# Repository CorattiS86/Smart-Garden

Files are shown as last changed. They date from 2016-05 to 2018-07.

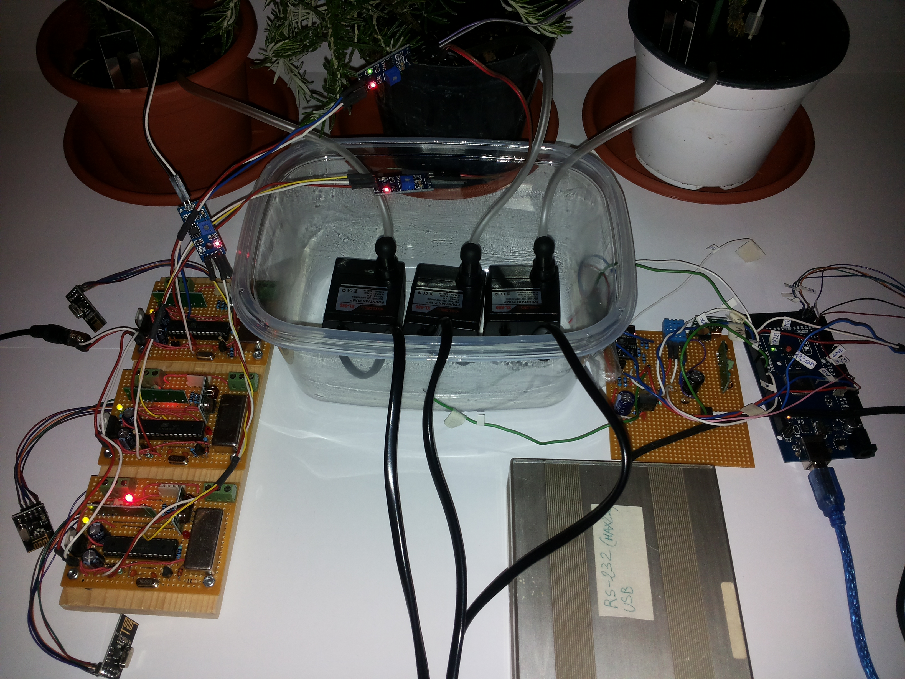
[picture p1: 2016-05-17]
Photos/system_2.jpg

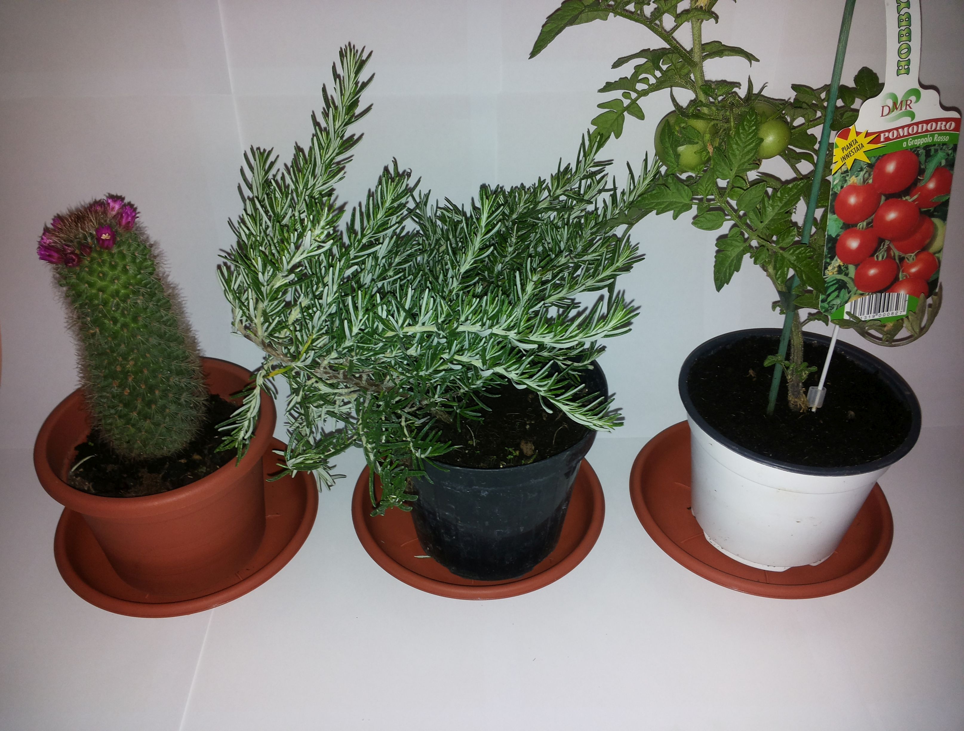
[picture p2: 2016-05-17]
Photos/plants.jpg

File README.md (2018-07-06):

# Smart-Garden
Pervasive Systems 2016 - DIAG "La Sapienza"
Stefano Coratti & Massimo Perri

In this repository there is all the material that describe how it was possible to build a system able to manage the watering of a garden.

The garden consists of 3 plants, for our choice we select:
 - Cactus plant
 - Rosemary plant
 - Tomato plant

The reason of such 3 plants is that they present 3 different characteristics from the point of view of watering.

For watering we decided to use flow irrigation. 
The biggest challenge in flow irrigation is accurately determining how much and when to water.

Based on a reasearch, that you can find in the follow link 

  "http://ucanr.edu/sites/scmg/files/30917.pdf" 
  
it is possible to see what influence irrigation for several kind of plant:
  - ET° (Evapotranspiration) factor
  - Crop coefficent
  - Density
  - Exposure factor
  - Planted area
  - Irrigation efficency
 
EVAPOTRANSPIRATION
Is the combined effect of soil water evaporation and plant water transpiration in the sorrounding environment, and values 
are provided in tables based on months for a specific location (latitude, proximity to the sea, etc...), referred 
to a reference crop ET° (grass).
We have found the table for own plant considering a mediterranean, center-south of italy environment.  

CROP COEFFICIENT
Crop coefficients, or species factors range from 0.1 to 0.9 and are
divided into four categories:
  - Very low      < 0.1 (10% of ET°)
  - Low       0.1 - 0.3 (10-30%)
  - Moderate  0.4 - 0.6 (40-60%)
  - High      0.7 - 0.9 (70-90%) 
 
PLANTING DENSITY
The planting density factor ranges in value from 0.5 to 1.3.
This range is separated into three categories:
  - Low—sparse                 0.5 - 0.9
  - Average—moderate coverage  1.0
  - High--complete coverage    1.1 - 1.3  
 
EXPOSURE FACTOR
The microclimate or exposure factor ranges from 0.5 to 1.4, and is divided into three categories: 
Average is open field, lowmoderate wind, part sun. Higher winds and greater exposure take a
higher factor, and a protected, shady location would use a lower factor.
  - Low     0.5 - 0.9
  - Average 1.0
  - High    1.1 - 1.4 
 
IRRIGATION EFFICENCY
Is related to the efficency of the kind of water erogator, in own implementation we assume 0.9 (90%) of efficency,
because the erogator hose is placed close to the roots.
 
Returning to what was said before, the choice of 3 plants is due to the fact that they have different values
of CROP EFFICENT and PLANTING DENSITY

|plant |crop coeff. | plant density | exposure factor | irrigation efficency |
|---|---|---|---|---|
| cactus | 0.2 | 1.0 | 1.0 | 0.9 | 
| rosemary  | 0.5 | 1.0 | 1.0 | 0.9 |
| tomato | 0.9 | 1.0 | 1.0 | 0.9 |

from which it is established a formula that says the amount of water necessary for the plant for a month

  (ET° x crop coeff. x density x exposure factor x planted area x .623) / (Irrigation efficiency)

such formula expresses the amount of water in gallons we translate such formula in liters, 
and use a conversion to compute daily amount of water. 

We use such informations to independently configure the 3 plants to obtain for each one an efficiently irrigation
using the least amount of water possible. 

Author
-----------------
Coratti Stefano

coratti.s86@gmail.com

https://www.linkedin.com/in/stefano-coratti-83005a85/

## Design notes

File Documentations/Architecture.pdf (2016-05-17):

## SMART GARDEN PROJECT

### Pervasive System 2016 – DIAG “La Sapienza” Stefano Coratti & Massimo Perri

ARCHITECTURE:

The Smart Garden is a system composed by many elaboration/processing nodes or station that are within a garden scenario with plants, where each plant has its own ‘plant computer’ and there is a unique ‘master’ station in the garden.

In the demo implementation a single master and three slave stations are provided. The stations create a wireless network, where each station has an address and plant stations can interact and exchange messages with the central master station. Master station transmit broadcast messages to all the slaves in the network and receive messages from the single slave stations to it.

The scope of the master station is providing timing broadcast sync messages and weather data, using readings from a number of sensors that capture the relevant environmental values (atmospheric pressure, temperature, humidity, light intensity) to the slave/plant stations.

Plant stations do synchronize with the master, receive data from it and perform each their own calculation and the intelligent decision algorithm, with as inputs the weather data received from the master and their own configuration, that depends on the kind of plants they provide water.

The general idea is that the master periodically sends a sync message with weather and configuration information to the slaves; the slaves keep receiving until they got the master sync message, extract info and use them as input to their internal watering algorithm, along with slave station specific configuration. On the base of results of the watering algorithm each slave station provide or not provide water to the associated plant and, also, calculate the right volume amount of water to use, issuing commands to a submersible water pump that pumps up the water to the plant from a tank.

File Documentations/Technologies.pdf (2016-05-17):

## SMART GARDEN PROJECT

### Pervasive System 2016 – DIAG “La Sapienza” Stefano Coratti & Massimo Perri

TECHNOLOGIES:

We used the following technologies in the Smart Garden project

Arduino, both the hardware platform (in the specific 1 Arduino Mega 2560 and 3 custom made Arduino-standalone ATMEGA328P@16Mhz) and the software one, means the Arduino IDE and programming language https://www.arduino.cc/

USPASP programmer hardware/driver , used to physically made in circuit programming on the slave stations by Arduino IDE http://www.fischl.de/usbasp/

USB-RS232+MAX232 interface & logic level converter to provide extra serial communication with the Arduino Mega for diagnostic and debug purposes https://en.wikipedia.org/wiki/MAX232

Blynk to provide in the cloud data forwarding and client app to Android/IOS devices, used to visualize actual data from the smart garden, including soil humidity levels at the plants http://www.blynk.cc/

ThingSpeak service for IoT to provide in the cloud data collection and graphic visualization of collected data points and also to trigger a react for generating email alerts using PushingBox web service https://thingspeak.com/

PushingBox service for IoT, an Internet based service to provide email sending from devices, in our case PushingBox actions are controlled directly by events captured at ThingSpeak data collection facility https://www.pushingbox.com/

ExtremeAVRBurner or avrdude AVR programming software: http://extremeelectronics.co.in/avrtutorials/gui-software-for-usbasp-based-usb-avr-programmers/ (http://extremeelectronics.co.in/avr-tutorials/gui-software-for-usbasp-based-usb-avr-programmers/) , http://www.nongnu.org/avrdude/ use one of these tools to program just once the ATmega328Ps fuse bits (required to make them run at 16Mhz clock external oscillator)

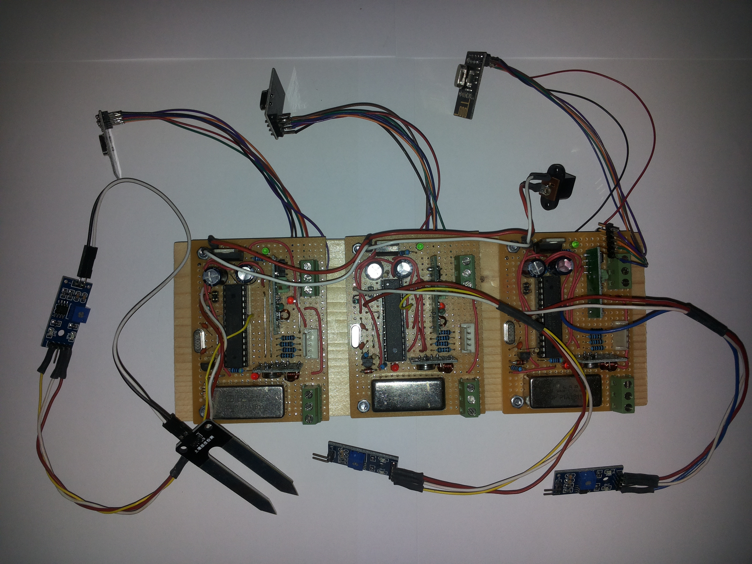
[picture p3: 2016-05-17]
Photos/slaves.jpg

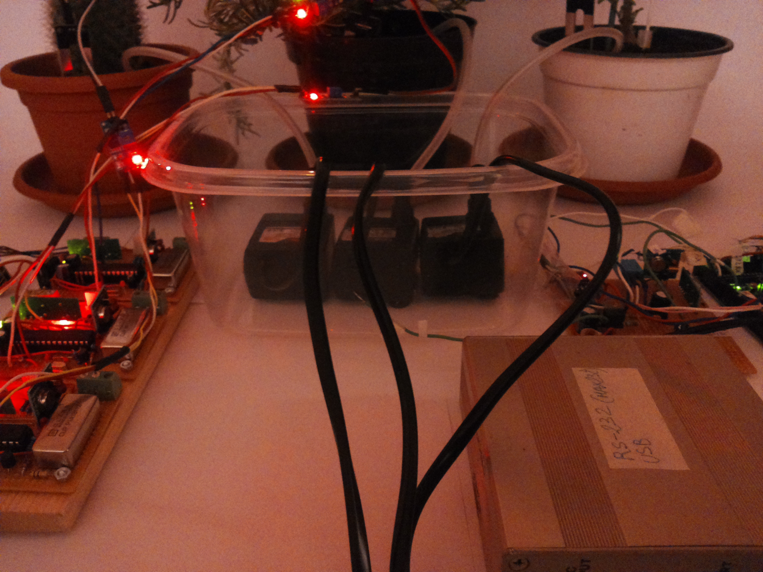
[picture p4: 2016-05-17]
Photos/system_3.jpg

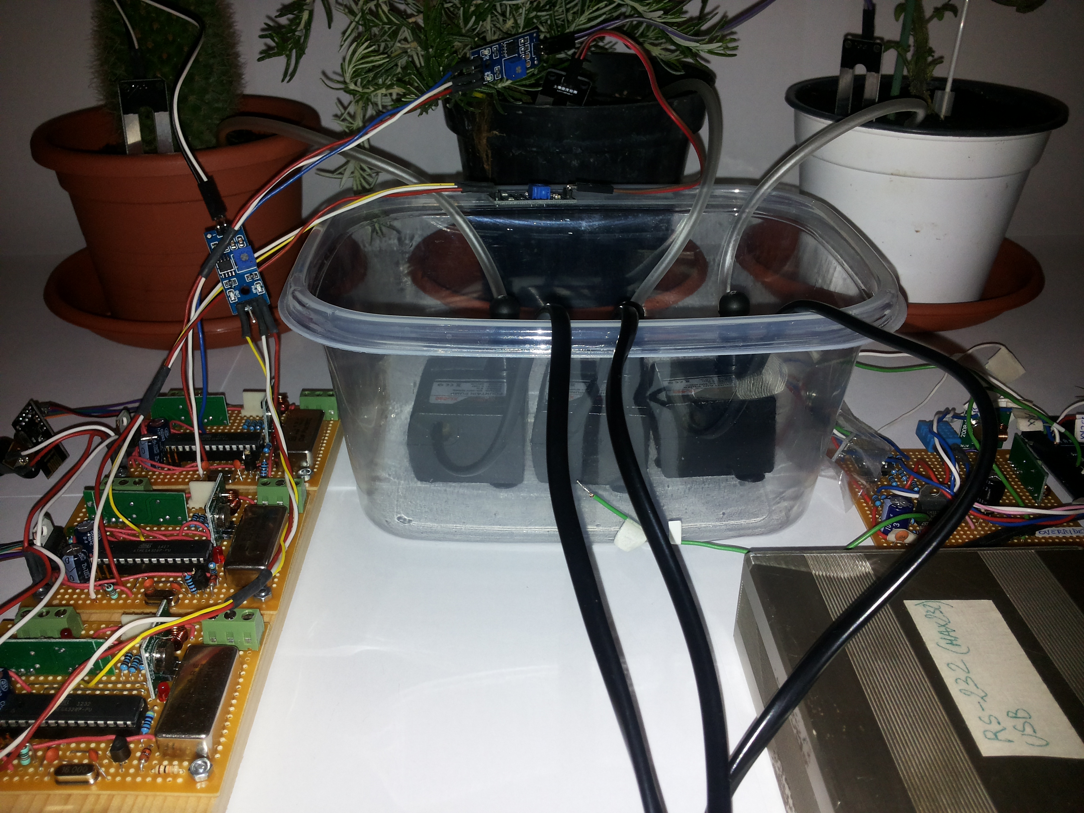
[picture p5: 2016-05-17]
Photos/system_1.jpg

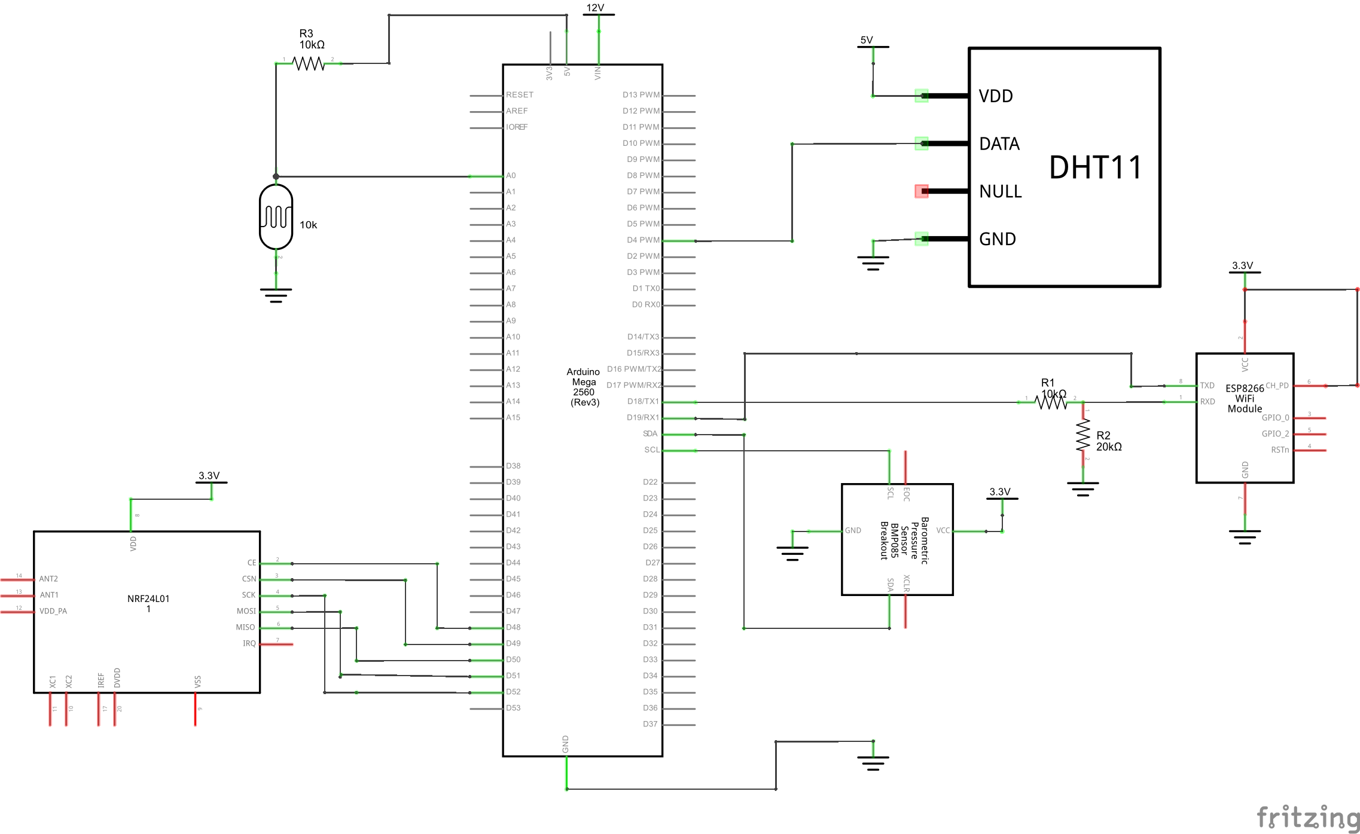
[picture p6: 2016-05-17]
Fritzing-Schemes/MASTER_schem.png

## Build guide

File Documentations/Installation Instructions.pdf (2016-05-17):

## SMART GARDEN PROJECT

### Pervasive System 2016 – DIAG “La Sapienza” Stefano Coratti & Massimo Perri

INSTALLATION INSTRUCTIONS

The replication of the system is a complex task that requires at least average electronic skills and , of course, a bit of familiarity with software and Arduino related hardware e.g. board, sensors , modules and shields.

Get the material, both hardware and software, in particular 3x ATmega328P and related components to make an arduino standalone @16Mhz (e.g. XTAL 16MHz, 2x 22pF caps, 10Kohm pullup resistor and the like) for this one can use as reference this web page: https://www.arduino.cc/en/Main/Standalone ; then also an Arduino Mega 2560 is required (mega 1280 can be used as well, and so also other similar boards with at least 3 hardware serials uart; software serials are not suitable for the project). Other support material is required e.g. an USB-TTL converter is highly suggested to have the diagnostic & debug serial communication with the PC; USB-RS232+MAX232 are also cheap and valid alternatives to USB-TTL converters. USBASP programmers can be built using e.g. ATmega8 or ATmega88 plus some other components or bought online or in electronic shops. Sensors needed are included in diagrams and schematics and are: one BMP180 (Bosh) , one DHT11, one 10K photoresistor for weather data; 3x Arduino soil hygrometer (HL-69 or the like) + 3x moisture sensor (HL-69, FC-28 or the like) + 3x 2-wires Dupont lines; 3x small 220v or 12v submersible water pump (e.g. 30l/h flow); as software Arduino IDE , USBASP driver, a terminal program e.g. Putty and libraries (e.g. Blynk and ESP8266) are required.

Build the sensor board and connect it to the Mega: use BMP180, DHT11, photoresistor, ESP8266 and nRF24L01 to build the board; use extra components for voltage level shifting and 3v3 volt line regulation. Program Arduino Mega with the master sketch and connect the sensor board to it.

Build the slave boards (plant computers) and connect to the pumps: make the slaves (you may use 3, or less or more that 3 changing the code accordingly) using ATmega328P and other components required e.g. relay and nRF24L01 module.

Program fuse bits using the ICSP connector, connecting the USBASP programmer and using avrdude or ExtremeAVRBurner: correct fuses bits settings are: low_fuses=0xff high_fuses=0xde extended_fuses=0x05

Program each slave using the ICSP connector and the USBASP programmer & Arduino IDE: to do that add a standalone configuration (as provided in point 4) to your Arduino IDE in the ‘boards.txt’ file under the installation directory. When all is ready connect the single boards to their water pump to test and use the system.

In ‘<your-arduino-ide-install-dir>\hardware\arduino\avr\ boards.txt’ add the following configuration for the Arduino standalone:

stand_alone_atmega328.name=ATmega328P (stand-alone @16MHz)

stand_alone_atmega328.build.board=ATmega328P_stand-alone_16MHz

stand_alone_atmega328.upload.using=usbasp

stand_alone_atmega328.upload.protocol=usbasp

stand_alone_atmega328.upload.tool=usbasp

stand_alone_atmega328.upload.params.quiet=true

stand_alone_atmega328.upload.protocol=stk500

stand_alone_atmega328.upload.maximum_size=32768

stand_alone_atmega328.upload.speed=57600

stand_alone_atmega328.bootloader.low_fuses=0xFF

stand_alone_atmega328.bootloader.high_fuses=0xDA

stand_alone_atmega328.bootloader.extended_fuses=0x05

stand_alone_atmega328.bootloader.path=atmega

stand_alone_atmega328.bootloader.unlock_bits=0x3F

stand_alone_atmega328.bootloader.lock_bits=0x0F

stand_alone_atmega328.build.mcu=atmega328p

stand_alone_atmega328.build.f_cpu=16000000L

stand_alone_atmega328.build.core=arduino:arduino

stand_alone_atmega328.build.variant=arduino:standard

Use a suitable water tank, put the pumps inside it and connect their output hoses to the plants: when ready for test/run fill the tank with water submersing the pumps

Switch on the Mega and slaves (slaves must be provided with external power source e.g. 5V or 12v powersupply with 5V regulator on board), connect pump power system (e.g. 12V battery or to a wall socket if pumps runs on poweline)

Connect USB cable to the Mega – if debug is required connect the USB-TTL (or RS232+MAX232) converter to another USB port

Open Terminal on Mega com port (es. COM10 if that is the port assigned to Mega): if debug needed launch the terminal on the com port of the usb-ttl converter too; then launch the startup script, this will trigger an automatic reset on the master, then initialization will follow, the master will init the WiFi module, then will get the timestamp from Blynk and proceed with the first broadcast sync message to the slaves. If debug terminal is active you could see messages from the master announcing the various phases transitions

Tweak parameters to suit your needs: switch on or off the email alerts, switch on or off the in cloud logging on ThingSpeak, change the plant computer configuration to be sent, etc. all this in the master sketch; also change idle delay to fix a maximum repetition rate e.g. 30 minutes , 60 minutes or the like as you need

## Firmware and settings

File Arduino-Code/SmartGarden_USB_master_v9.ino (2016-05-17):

//////////////////////////////////////////////////////////////////////////////////////////////////
//                                                                                              //
//                                      SMART GARDEN PROJECT                                    //
//                                                                                              //
//                           for Pervasive Systems 2016 @ DIAG Sapienza                         //
//                                http://persys2016-diag.slack.com/                             //
//                                                                                              //
//                                 Stefano Coratti & Massimo Perri                              //
//                                                                                              //
//                                                                                              //
// MASTER program, target board: Arduino Mega 2560                                              //
//////////////////////////////////////////////////////////////////////////////////////////////////
//#define BLYNK_NO_INFO
//#define BLYNK_DEBUG
#include <BlynkSimpleSerial.h>
#include <Wire.h>
#include <Adafruit_Sensor.h>
#include <Adafruit_BMP085_U.h>
#include <RHReliableDatagram.h>
#include <RH_NRF24.h>
#include <SPI.h>
#include <TimeLib.h>
#include <WidgetRTC.h>



/* auth token */
char auth[ ] = "6a0cd1a204764d21a1930c8a3476c86d";

//boolean online_alerts = false; //if true online alerts via email by PushingBox will be enabled
//boolean online_logging = false; //if true ThinkSpeak logging will be enabled
boolean online_alerts = true; //if true online alerts via email by PushingBox will be enabled
boolean online_logging = true; //if true ThinkSpeak logging will be enabled

//temp & pressure sensor BMP180
Adafruit_BMP085_Unified bmp = Adafruit_BMP085_Unified(10085);

//DHT111
#include <dht.h>
dht DHT;
#define DHT11_PIN 4
       
#define BLYNK_PRINT Serial

WidgetRTC rtc;
BLYNK_ATTACH_WIDGET(rtc, V5);

#define TIME_HEADER  "T"   
#define TIME_REQUEST  7    

#define SERVER_ADDRESS 254
// Singleton instance of the radio driver
//RH_NRF24 driver;
// RH_NRF24 driver(8, 7);   // For RFM73 on Anarduino Mini
RH_NRF24 driver(48,49);
// Class to manage message delivery and receipt, using the driver declared above
RHReliableDatagram manager(driver, SERVER_ADDRESS);

int RECV_INTERVALS = 5; //20 receive intervals -> 20 seconds of rx
int IDLE_DELAY = 15000; //the delay between web/process and next loop in milliseconds

/* override demo values */
float  DEMO_TEMP = 46.0;
int DEMO_HUMIDITY = 10; 
boolean override_flag = false;

long debouncing_time = 15; //Debouncing Time in Milliseconds
volatile unsigned long last_micros;


//////////////// WIFI ESP8266 //////////////////

#include "ESP8266.h"

#define SSID        "TIM_ID445"
#define PASSWORD    "!@Taipei101$$"
#define HOST_NAME   "api.thingspeak.com"
#define HOST_PORT   (80)

ESP8266 wifi(Serial2,115200);

void ESP8266setup(void)
{
    Serial1.print("setup begin\r\n");

    Serial1.print("FW Version:");
    Serial1.println(wifi.getVersion().c_str());

    if (wifi.setOprToStationSoftAP()) {
        Serial1.print("to station + softap ok\r\n");
    } else {
        Serial1.print("to station + softap err\r\n");
    }

    if (wifi.joinAP(SSID, PASSWORD)) {
        Serial1.print("Join AP success\r\n");

        Serial1.print("IP:");
        Serial1.println( wifi.getLocalIP().c_str());       
    } else {
        Serial1.print("Join AP failure\r\n");
    }

    for(int x = 0; x<10; x++) //retry 10 times before giving up
    if (wifi.disableMUX()) {
        Serial1.print("single ok\r\n");
        x=10; //exit
    } else {
        Serial1.print("single err\r\n");
    }
    
    Serial1.print("ESP8266 setup end\r\n");
}

void sendNotification()
{
  uint8_t buffer[1024] = {0};

    for(int x = 0; x<10; x++) //retry 10 times before giving up
    if (wifi.createTCP(HOST_NAME, HOST_PORT)) {
        Serial1.print("create tcp ok\r\n");
        x=10; //exit
    } else {
        Serial1.print("create tcp err\r\n");
    }

    delay(500);

    //char *hello = "GET / HTTP/1.1\r\nHost: api.thingspeak.com/update?api_key=J2UBCQ8WHN4ISS1M&field8=0\r\nConnection: close\r\n\r\n";

    char *hello = "GET /update?api_key=J2UBCQ8WHN4ISS1M&field8=0\r\n\r\n"; 

    //char *hello = "GET / HTTP/1.1\r\nHost: www.google.com\r\nConnection: close\r\n\r\n";
    
    wifi.send((const uint8_t*)hello, strlen(hello));

    uint32_t len = wifi.recv(buffer, sizeof(buffer), 20000);
    if (len > 0) {
        Serial1.print("Received:[");
        for(uint32_t i = 0; i < len; i++) {
            Serial1.print((char)buffer[i]);
        }
        Serial1.print("]\r\n");
    }

    /*
    delay(100);

    if (wifi.releaseTCP()) {
        Serial1.print("release tcp ok\r\n");
    } else {
        Serial1.print("release tcp err\r\n");
    }
    */
}

void sendThingSpeakUpdate(String s)
{
  uint8_t buffer[1024] = {0};

    //for(int x = 0; x<10; x++) //retry 10 times before giving up

    delay(500);
    if (wifi.createTCP(HOST_NAME, HOST_PORT)) {
        Serial1.print("create tcp ok\r\n");
        //x=10; //exit
    } else {
        Serial1.print("create tcp err\r\n");
    }

    delay(500);

    char * hello = new char[s.length() + 1];

    strcpy(hello,s.c_str());

    wifi.send((const uint8_t*)hello, strlen(hello));

    
    uint32_t len = wifi.recv(buffer, sizeof(buffer), 2000);
    if (len > 0) {
        Serial1.print("Received:[");
        for(uint32_t i = 0; i < len; i++) {
            Serial1.print((char)buffer[i]);
        }
        Serial1.print("]\r\n");
    }
    

    /*
    delay(300);

    if (wifi.releaseTCP()) {
        Serial1.print("release tcp ok\r\n");
    } else {
        Serial1.print("release tcp err\r\n");
    }
    */
}


/* data structures */

struct dataStruct{
  time_t timestamp;

  float press_atm;
  float temp;
  byte humidity;
  int light_intensity;

  /* dafault config values for the three plants */
  int s_1_humidity_th = 200;  //max th above of this value no water will be provided (to prevent mould and root problems)
  int s_1_max_cm3_week = 400; //max water volume in the week (cm3)

  int s_2_humidity_th = 300;
  int s_2_max_cm3_week = 800;

  int s_3_humidity_th = 500;
  int s_3_max_cm3_week = 1200;

  boolean override_s = false;

}myData;

byte tx_buf[sizeof(myData)] = {0};

struct dataSlave_1{
  time_t timestamp;
  
  int soil_humidity = 0;
}slaveData_1;

struct dataSlave_2{
  time_t timestamp;
  
  int soil_humidity = 0;
}slaveData_2;

struct dataSlave_3{
  time_t timestamp;
  
  int soil_humidity = 0;
}slaveData_3;


//Lux calculation routine
double Light (int RawADC0)
{
  double Vout=RawADC0*0.0048828125;
  //int lux=500/(10*((5-Vout)/Vout));//use this equation if the LDR is in the upper part of the divider
  int lux=(2500/Vout-500)/10;
  return lux;
}

/* read weather data and store them in local data structure */
void readWeatherData()
{
   ///read sensors
    /* Get a new sensor event */ 
      sensors_event_t event;
      bmp.getEvent(&event);
     
      /* Display the results (barometric pressure is measure in hPa) */
      if (event.pressure)
      {

        float pressure_atm = 0.0;
        bmp.getPressure(&pressure_atm); 
        pressure_atm/=1000;  //convert the value to kPa
        myData.press_atm=pressure_atm;
        /* Display atmospheric pressue in hPa */
        /*
        Serial1.print("Pressure:    ");
        Serial1.print(pressure_atm);
        Serial1.println(" hPa");
        */
        
        /* First we get the current temperature from the BMP085 */
        float temperature;
        bmp.getTemperature(&temperature); //in °C
        myData.temp = temperature;
        /*
        Serial1.print("Temperature: ");
        Serial1.print(temperature);
        Serial1.println(" C");
        */

        //read air relative humidity
        int chk = DHT.read11(DHT11_PIN);
        myData.humidity = DHT.humidity;
        
        //read light intensity, pin A0 for the LDR and covert to lux
        myData.light_intensity = (int)(Light(analogRead(0)));     
      }
      else
      {
        //Serial1.println("Sensor error");
      }

}

/* put values on Blynk */
void pushWeatherData()
{    
        Blynk.virtualWrite(1, myData.press_atm);               
        Blynk.virtualWrite(2, myData.temp);
        Blynk.virtualWrite(3, myData.humidity);
        Blynk.virtualWrite(4, myData.light_intensity);
}

/* push slaves data to Blynk for e.g. display */
void pushSlavesData()
{
 Blynk.virtualWrite(6, slaveData_1.soil_humidity); 
 Blynk.virtualWrite(7, slaveData_2.soil_humidity); 
 Blynk.virtualWrite(8, slaveData_3.soil_humidity); 
}

/* process data and update web info */
void processAndSendData()
{
  //push data to Blink..
  pushWeatherData();
  //update slaves data and push to Blink
  pushSlavesData();
}

boolean boo = true;


/* handle override pin change */
void checkPin()
{
  // Invert state, since button is "Active LOW"
  if (!digitalRead(2))
  {
    boo=!boo;
    override_flag = boo;
    
    if(override_flag)
    digitalWrite(13, HIGH); else digitalWrite(13, LOW);
  }
}

void debounceInterrupt() {
  if((long)(micros() - last_micros) >= debouncing_time * 1000) {
    checkPin();
    last_micros = micros();
  }
}

////TIME

void digitalClockDisplay(){
  // digital clock display of the time
  Serial1.print(hour());
  printDigits(minute());
  printDigits(second());
  Serial1.print(" ");
  Serial1.print(day());
  Serial1.print(" ");
  Serial1.print(month());
  Serial1.print(" ");
  Serial1.print(year()); 
  Serial1.println(); 
}

void printDigits(int digits){
  // utility function for digital clock display: prints preceding colon and leading 0
  Serial1.print(":");
  if(digits < 10)
    Serial1.print('0');
  Serial1.print(digits);
}


void processSyncMessage() {
  unsigned long pctime;
  const unsigned long DEFAULT_TIME = 1462663749; // 7 maggio 2016

  if(Serial1.find(TIME_HEADER)) {
     pctime = Serial1.parseInt();
     if( pctime >= DEFAULT_TIME) { // check the integer is a valid time (greater than Jan 1 2013)
       setTime(pctime); // Sync Arduino clock to the time received on the serial port
     }
  }
}

time_t requestSync()
{
  Serial1.write(TIME_REQUEST);  
  return 0; // the time will be sent later in response to serial mesg
}

///





// the setup function runs once when you press reset or power the board
void setup() {
    Serial1.begin( 115200 );  //for debug/logging

    Serial1.println("MASTER ESP8266 WIFI config init..");

    ESP8266setup();

    //now procede on
    
    override_flag = false; 
    
    if (!manager.init()) //init the manager.. and check
    {
     //Serial1.println("nRF24L01 init failed");
    }
    /* A0 as analog input for the LDR */
    pinMode(A0, INPUT);

    //override led, on if active, pin 13
    pinMode(13, OUTPUT);
    
    /* override PIN handling */
    // Make pin 2 HIGH by default
    pinMode(2, INPUT_PULLUP);
    // Attach INT to our handler
    attachInterrupt(digitalPinToInterrupt(2), debounceInterrupt, FALLING);

    /* Initialise the BMP180 sensor */
      if(!bmp.begin())
      {
        /* There was a problem detecting the BMP085 ... check your connections */
        Serial1.print("Ooops, no BMP085 detected ... Check your wiring or I2C ADDR!");
        while(1);
      }
      
    
    Serial.begin( 115200 );
    Blynk.begin( auth,115200); 

    while (Blynk.connect() == false) {
      // Wait until connected
    }

   // Begin synchronizing time using RTC
   rtc.begin();
}


// the loop function runs over and over again until power down or reset
void loop() 
{
  Serial1.println("MASTER started: waiting for timestamp");
  while (timeStatus()== timeNotSet)  //wait until time is set..
  {
    Blynk.run();
  }
  Serial1.println("got timestamp..");
  //read weather data, store into data structure
  readWeatherData();
  
  //set actual timestamp in data structure and send broadcast with weather data, config and override
  if (timeStatus()!= timeNotSet) //here must be true
  { 
        //set timestamp
        myData.timestamp = now();

        Serial1.print("timestamp: ");
        Serial1.println(myData.timestamp);
        /* OVERRIDE HANDLING */
        if(override_flag) //give demo data and set override_s to true
        {
          myData.temp = DEMO_TEMP;
          myData.humidity = DEMO_HUMIDITY;
          myData.override_s = true;

         //override set, send notification via email by PushBox
         if(online_alerts) sendNotification();
        }
        else
           {
            myData.override_s = false; 
           }
        Serial1.print("override_s :");   
        Serial1.println(myData.override_s);  
        
        memcpy(tx_buf, &myData, sizeof(myData) );
        byte zize=sizeof(myData);
  
        //sending BC
        Serial1.println("");
        Serial1.println("sending SYNC broadcast..\n");
        //send SYNC broadcast
        manager.sendtoWait((uint8_t *)tx_buf, zize, 0xFF);

       
        /*
        if (manager.available())
        {
          if (!manager.sendtoWait((uint8_t *)tx_buf, zize, 0xFF))
              Serial1.println("sendtoWait failed");
          //reset override_flag
          
        }
        */

  }
  
  ///then it looks for msgs from slaves
  uint8_t buf[RH_NRF24_MAX_MESSAGE_LEN];
  uint8_t buflen = sizeof(buf);
  uint8_t from;

  
  for(int t = 0; t<RECV_INTERVALS; t++) //receive for RECV_INTERVALS times
  {
  if (manager.recvfromAckTimeout(buf, &buflen, 1000, &from))
  { 
        // Message with a good checksum received, dump it.
        Serial1.println("");
        Serial1.print("Got msg from slave addr: ");
        Serial1.print(from,DEC); 
        Serial1.print(" ");
        Serial1.print("msg size : ");
        Serial1.print(buflen, DEC);

        //copy data in the right data structure..
        if(from == 1) //slave 1
        {
         memcpy(&slaveData_1, buf, sizeof(slaveData_1));
         Serial1.println("");
       
         Serial1.print("timestamp: ");
         Serial1.print(slaveData_1.timestamp);

         Serial1.print(" soil_humidity: ");
         Serial1.print(slaveData_1.soil_humidity);
        }
       if(from == 2) //slave 2
        {
         memcpy(&slaveData_2, buf, sizeof(slaveData_2));
         Serial1.println("");
       
         Serial1.print("timestamp: ");
         Serial1.print(slaveData_2.timestamp);

         Serial1.print(" soil_humidity: ");
         Serial1.print(slaveData_2.soil_humidity);
        } 
        if(from == 3) //slave 3
        {
         memcpy(&slaveData_3, buf, sizeof(slaveData_3));
         Serial1.println("");
       
         Serial1.print("timestamp: ");
         Serial1.print(slaveData_3.timestamp);

         Serial1.print(" soil_humidity: ");
         Serial1.print(slaveData_3.soil_humidity);
        } 
   
   }
  }//for
  

  Serial1.println("");
  Serial1.println("process and send data..\n");
  //process data / send to the web
  //push them to Blynk
  processAndSendData();

  //push data to ThingSpeak for temporal dynamics graphs
  /*
  float press_atm;
  float temp;
  byte humidity;
  int light_intensity;
  
  int soil_humidity
  */
  String str = "GET /update?api_key=J2UBCQ8WHN4ISS1M&field1="+(String)myData.press_atm+"&field2="+(String)myData.temp+"&field3="+(String)myData.humidity+"&field4="+(String)myData.light_intensity+"&field5="+(String)slaveData_1.soil_humidity+"&field6="+(String)slaveData_2.soil_humidity+"&field7="+(String)slaveData_3.soil_humidity+"\r\n\r\n";
  
  if(online_logging) sendThingSpeakUpdate(str);

  Serial1.println("");
  Serial1.println("idle..\n");
  //wait in idle mode
  delay(IDLE_DELAY);

    
    
  Blynk.run();
}
